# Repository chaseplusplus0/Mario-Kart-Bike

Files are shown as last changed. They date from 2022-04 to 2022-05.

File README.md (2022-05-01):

# MarioKart Bike Executive Summary

The MarioKart exercise bike project was an attempt to create an enjoyable and practical method of combining the benefits of aerobic exercise with the fun of playing a racing video game. The idea was to make physical activity easier and more desirable through the medium of gaming in a notably novel way. Using various external control systems attached to a standard bicycle, the goal was to turn a bike into a resistive-style exercise machine and a modified Nintendo Switch controller. The main functions desired for this system included functional steering translation, tire acceleration/RPM measurement, convenient buttons for other game functions (i.e. drifting, braking, item usage, menu navigation), and a microcontroller driven resistive element for the exercise portion. Ideally, these would all function with minimal user intervention so that the player can simply connect the controller and begin racing. The placement of the control options and various systems on the bike would be in safe, out of the way locations such that the user would not need to worry about any connections, mechanical obstacles, or malfunctions when using the bike in the standard fashion. Additionally, there was a design in place for an integrated health monitoring system to aid the user in finding out calories burned during play. The system as a whole was meant to be simple and streamlined such that almost anyone could hop on and start playing quickly.

# Current Capabilities

As of the latest contributions to the repo, the project functions minimally in all fields. Each subsystem planned in the design drafts has been implemented in some recognizable form. The capabilities of each system can be found in their individual files with much more detail.

### Controls

The control systems for steering, acceleration, drifting, and item throwing are all in place and playable. They are of high enough fidelity that consistently playing and winning competitive races is very much possible with a little practice. The connection is with the Nintendo Switch over bluetooth, and once connected the bike can be used much like a standard Pro Controller. There are rudimentary menu buttons in place on the RPi touchscreen for navigation, but their functions is not yet complete. Current menu navigation must be done via the touchscreen of the Nintendo Switch.

### Resistance

The resistance subsystem has gone through many different iterations of design and testing. The one contained within the repo governs a quick-switch relay setup that causes a very brief short in the leads of the motor, acting as a quick brake force which slows the user down. The intention was to have this trigger during certain in-game events, but due to difficulty reading game/vibration data back from the console, this is done at random intervals.

### Health Monitoring

The health system functions according to an MET equation that takes in the user's weight and the length of time activity is being performed. The user enters the information and starts a timer via an RPi touchscreen GUI and then stops the clock when the race is finished, after which they can obtain the caloric burn data.

# Salient Outcomes

The most important outcomes of the final version of this project include the functional control scheme, the basic resistance system, and the basic health system. These systems represent the core intentions of the project itself. The control system works perfectly well to play a race in-game. Steering, acceleration, drifting, and item throwing are all present and work great, allowing for an entirely plausible simulation of a controller. The resistance system is subtle, but effective at forcing the user to pedal a bit harder in certain stages. This in addition to the base resistance introduced by connecting the motor to the flywheel driven by the bike tire creates a solid workout that isn't too difficult to play through multiple races with. Additionally, it has been noted that most people hardly notice the exercise during gameplay due to being distracted by the enjoyment of the game, only mentioning the burn afterwards. This was one of the major goals of the project in general. Lastly, the MET health system is simple to operate and informative, making the process of calorie burn estimation easy for the user to gauge if desired.

# Video Demonstration and Photo Documentation

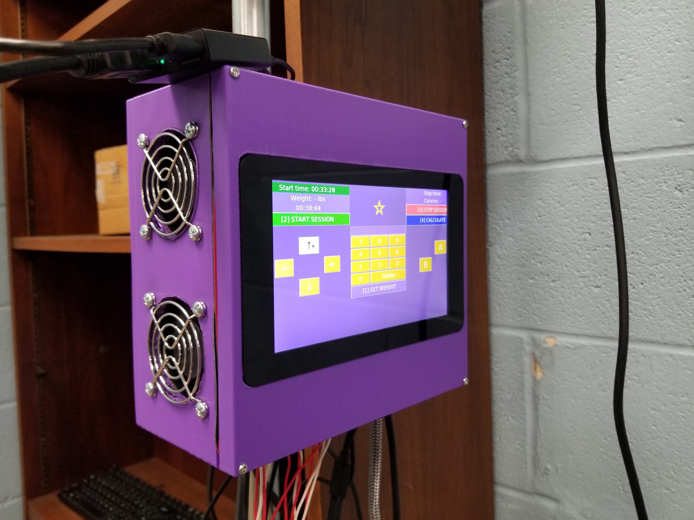
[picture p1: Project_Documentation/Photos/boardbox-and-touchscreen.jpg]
Video Video Demo (https://drive.google.com/file/d/1XO-LJ3wKvhisHmPTuDnR830Og8hAM-FM/view?usp=sharing)


Click the above picture to see the video demonstration of the project.

# About us

This was a 3 person capstone project at Tennessee Technological University that took place over the course of two semesters of class. Team members include Reed Hester, Leah Faulkner, and Chase Griffin. Reed Hester is an Electrical Engineer and a graduating senior, and he worked mostly on the physical frame, modelling, and resistive element of the design. Chase Griffin is a Computer Engineer and also a graduating senior, and he worked on developing the control systems, implementing the component and sensor systems on the bike, and writing the programs to both operate and control the components and communicate with the Nintendo Switch/MarioKart game. Leah Faulkner is also a Computer Engineer, and she worked on the MET health system equations, touchscreen GUI controls, and the board box fan/airflow improvement. The supervising faculty member on this project was Jesse Roberts, and he proposed the original idea for the project itself. There was no direct customer for this project, and the intended userbase was very broad.

# Repo Contents

This repository contains various bits of code used in the Mario Kart Bike capstone project. There are two Arduino files, one python program for the GUI, and one larger python program that collects data from every external system and converts it to controller data.

### Arduino Files

There are two Arduino compatible programs created for the two Arduino Nanos utilized in this project. The tachometer program contains the code necessary to operate the IR object-detection unit and to calculate the RPM from said unit. The motor control program contains the code to run the relay-controlled motor resistance system.

### MET and GUI Program

There is a python program that contains the code for the GUI that operates the health system and the menu navigation buttons.

### Joycontrol Python Program

This program is what does the actual control translation from each of the control systems on the bike. It is based on the open-source "Joycontrol" github program which can be found [here](https://github.com/mart1nro/joycontrol).

However, a specific branch was used for the applications of this project, which can be instead found [here](https://github.com/Poohl/joycontrol).

### Project Reports

The reports from the project proposal and phase 1 and 2 of design are contained in this repo in pdf form to give perspective on the entire design process from start to finish. They outline each step from conceptualization of the subsystems and initial specifications to the final version of each component and sensor being used in the build. It also contains the rationale behind each design choice, why some portions were removed from the scope, and why the bike exists in the state it does currently.

### Datasheet

There is a datasheet containing the interface and control details of each subsystem and how they interact with each other. It can serve as a general outline for how to use the system itself. There is also experimental data for each system present as well.

### Design Artifacts and BOM

The 2D schematics and 3D models used in the development of this project are also included as well to give a perspective on what was involved in the design process. There is a bill of materials that also shows the cost of every relevant component and structure used.

### Photos and Video

There are some pictures of the bike and its various components as well as a video of the completed project in working form.

# Final Notes

If there are any questions regarding certain parts of the bike construction or code function, please feel free to reach out here on Github or email me (Chase) at: chgriffin13@gmail.com

I'll do my best to help clarify!

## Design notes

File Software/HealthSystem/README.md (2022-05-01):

# What does it do?

This program generates the GUI for the MET health system and menu navigation buttons. It creates a graphical layout for the RPi touchscreen with several buttons, a keypad, and several display labels that allow the user to enter data for the caloric burn calculation as well as achieve basic menu navigation in the game during menu sequences.

# Dependencies

This program was written in Python 3 using the Tkinter toolkit to build the GUI. Tkinter is a part of the Python 3 library by default. It was written and formatted explicitly for the RPi 7" touchscreen module, but it can work without it using the desktop RPi controls.

# Installation

To install this program, simply clone the file and make sure Python 3 is installed on the computer. Additionally, if using the touchscreen, make sure the driver is up to date.

# Usage

To use, ensure the touchscreen is connected to the RPi, and then run the program. The GUI can be moved into place in the middle of the screen manually from the desktop if it does not fit. The RPi should also have a calibration feature in the settings if the touch does not seem to be in the right place. The keypad and corresponding weight and age buttons allow user data entry. The start and stop buttons control the timer. The calculation is performed on the stop of the timer. When using for a race measurement, simply enter the weight and age data, and then start the timer at the beginning of the race. When the race is over, hit stop, and your calorie burn count should be displayed. The menu buttons work like the standard d-pad and a/b buttons of a controller and can be used as such when connected to the game. Make sure all of the jumpers on the RPi are connected on the right pins to ensure these buttons will work.

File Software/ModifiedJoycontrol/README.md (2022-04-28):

# What does it do?

This file contains the modified version of the "Joycontrol" program used in our project. It serves as the primary control signal compiler, translator, and transmitter between the external control systems and the console/game. It runs on the RPi and connects to the Nintendo Switch via bluetooth. It is meant to simulate the datastream from a standard pro controller such that the Switch recognizes it as one.

# Dependencies

There are several dependencies to get this program working properly. First of all, it is only configured to run on the RPi 3/3B+ and cannot be guaranteed to work on other RPi device (although it technically should). It is running on the Raspian (RPi OS : Rapsian GNU/Linux 11 (bullseye)) Operating System. It also requires python3 to run the program itself as that is the language used for almost all files.

**Python** : [www.python.org/downloads](www.python.org/downloads)

As far as the libraries used within the program, many of them are detailed in the original README contents below, but there are a few additional ones required for the modifications.

If you don't already have pip:

	sudo apt install python3-pip

**GPIO Zero** : [Documentation](https://gpiozero.readthedocs.io/en/stable/index.html)

In RPi terminal:
	
	sudo apt update
	sudo apt install python3-gpiozero

**ADS1015 ADC library** : [https://github.com/adafruit/Adafruit_Blinka](https://github.com/adafruit/Adafruit_Blinka)

In RPi terminal:

	sudo pip3 install Adafruit-Blinka

Libraries in code:
	
	import board
	import busio
	import adafruit_ads1x15.ads1015 as ADS
	from adafruit_ads1x15.analog_in import AnalogIn

**Pyserial** :

	python3 -m pip install pyserial

Libraries in code:

	import serial

INSTALLATION AND USAGE PARAMETERS DEFINED BELOW

# Original README Contents
***

# joycontrol

Branch: master->amiibo_edits

Emulate Nintendo Switch Controllers over Bluetooth.

Tested on Raspberry 4B Raspbian, should work on 3B+ too and anything that can do the setup.

## Features
Emulation of JOYCON_R, JOYCON_L and PRO_CONTROLLER. Able to send:
- terminal button commands
- stick state
- nfc for amiibo read & owner registration 
- GPIO and serial compatibility
- Touchscreen button integration

## Installation
- Install dependencies  
  Raspbian:
```bash
sudo apt install python3-dbus libhidapi-hidraw0 libbluetooth-dev bluez
```
  Python: (a setup.py is present but not yet up to date)  
  Note that pip here _has_ to be run as root, as otherwise the packages are not available to the root user.
```bash
sudo pip3 install aioconsole hid crc8
```
 If you are unsure if the packages are properly installed, try running `sudo python3` and import each using `import package_name`.

- setup bluetooth
  - [I shouldn't have to say this, but] make sure you have a working Bluetooth adapter\
  If you are running inside a VM, the PC might but not the VM. Check for a controller using `bluetoothctl show` or `bluetoothctl list`. Also a good indicator it the actual os reporting to not have bluetooth anymore.
  - disable SDP [only necessary when pairing]\
  change the `ExecStart` parameter in `/lib/systemd/system/bluetooth.service` to `ExecStart=/usr/lib/bluetooth/bluetoothd -C -P sap,input,avrcp`.\
  This is to remove the additional reported features as the switch only looks for a controller.\
  This also breaks all other Bluetooth gadgets, as this also disabled the needed drivers.
  - disable input plugin [experimental alternative to above when not pairing]\
  When not pairing, you can get away with only disabling the `input` plugin, only breaking bluetooth-input devices on your PC. Do so by changing `ExecStart` to `ExecStart=/usr/lib/bluetooth/bluetoothd -C -P input` instead.
  - Restart bluetooth-deamon to apply the changes:
  ```bash
    sudo systemctl daemon-reload
    sudo systemctl restart bluetooth.service
  ```
  - see [Issue #4](https://github.com/Poohl/joycontrol/issues/4) if despite that the switch doesn't connect or disconnects randomly.

## Command line interface example
There is a simple CLI (`sudo python3 run_controller_cli.py`) provided with this app. Startup-options are:
```
usage: run_controller_cli.py [-h] [-l LOG] [-d DEVICE_ID]
                             [--spi_flash SPI_FLASH] [-r RECONNECT_BT_ADDR]
                             [--nfc NFC]
                             controller

positional arguments:
  controller            JOYCON_R, JOYCON_L or PRO_CONTROLLER

optional arguments:
  -h, --help            show this help message and exit
  -l LOG, --log LOG     BT-communication logfile output
  -d DEVICE_ID, --device_id DEVICE_ID
                        not fully working yet, the BT-adapter to use
  --spi_flash SPI_FLASH
                        controller SPI-memory dump to use
  -r RECONNECT_BT_ADDR, --reconnect_bt_addr RECONNECT_BT_ADDR
                        The Switch console Bluetooth address (or "auto" for
                        automatic detection), for reconnecting as an already
                        paired controller.
  --nfc NFC             amiibo dump placed on the controller. Equivalent to
                        the nfc command.

```

To use the script:
- start it (this is a minimal example)
```bash
sudo python3 run_controller_cli.py PRO_CONTROLLER
```
- The cli does sanity checks on startup, you might get promps telling you they failed. Check the command-line options and your setup in this case. (Note: not the logging messages). You can however still try to proceed, sometimes it works despite the warnings.

- Afterwards a PRO_CONTROLLER instance waiting for the Switch to connect is created.

- If you didn't pass the `-r` option, Open the "Change Grip/Order" menu of the Switch and wait for it to pair.

- If you already connected the emulated controller once, you can use the reconnect option of the script (`-r <Switch Bluetooth Mac address>`). Don't open the "Change Grip/Order" menu in this case, just make sure the switch is turned on. You can find out a paired mac address using the `bluetoothctl paired-devices` system command or pass `-r auto` as address for automatic detection.

- After connecting, a command line interface is opened.  
  Note: Press \<enter> if you don't see a prompt.

  Call "help" to see a list of available commands.

## API

See the `run_controller_cli.py` for an example how to use the API. A minimal example:

```python
from joycontrol.protocol import controller_protocol_factory
from joycontrol.server import create_hid_server
from joycontrol.controller import Controller

# the type of controller to create
controller = Controller.PRO_CONTROLLER # or JOYCON_L or JOYCON_R
# a callback to create the corresponding protocol once a connection is established
factory = controller_protocol_factory(controller)
# start the emulated controller
transport, protocol = await create_hid_server(factory)
# get a reference to the state beeing emulated.
controller_state = protocol.get_controller_state()
# wait for input to be accepted
await controller_state.connect()
# some sample input
controller_state.button_state.set_button('a', True)
# wait for it to be sent at least once
await controller_state.send()
```

## Issues
- Some bluetooth adapters seem to cause disconnects for reasons unknown, try to use an usb adapter or a raspi instead.
- Incompatibility with Bluetooth "input" plugin requires it to be disabled (along with the others), see [Issue #8](https://github.com/mart1nro/joycontrol/issues/8)
- The reconnect doesn't ever connect, `bluetoothctl` shows the connection constantly turning on and off. This means the switch tries initial pairing, you have to unpair the switch and try without the `-r` option again.
- ...

## Thanks
- Special thanks to https://github.com/dekuNukem/Nintendo_Switch_Reverse_Engineering for reverse engineering of the joycon protocol
- Thanks to the growing number of contributers and users

## Resources

[Nintendo_Switch_Reverse_Engineering](https://github.com/dekuNukem/Nintendo_Switch_Reverse_Engineering)

[console_pairing_session](https://github.com/timmeh87/switchnotes/blob/master/console_pairing_session)

[Hardware Issues thread](https://github.com/Poohl/joycontrol/issues/4)

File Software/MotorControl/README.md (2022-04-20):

# What does it do?

The motor resistance control program is incredibly simple. It has gone through many iteration, and some skeleton code from the old systems remains in comments in case those systems are ever revisited. Currently, the operating code governs a relay connected to the leads of the DC motor. This program quickly closes and opens the relay at random time intervals (between 10 and 45 seconds). It was meant to only trigger upon recieving serial data from the RPi that contained the vibration state of the controller recieved from the game. This condition, however, turned out to be redundant because the vibration state returned was always high, meaning the trigger happened repeatedly at all times. To save serial bus space for the RPi, this condition was removed, and now the trigger happens simply randomly.

# Dependencies

This program was designed for the Arduino Nano and a relay component. Without modifying pin connections, it will only work with these components. All functions present are found within the Arduino IDE. It is programmed in C++.

# Installation

To install this program, just open the Arduino file in the IDE, connect the Arduino Nano via USB to your computer, select the right board and port settings in the IDE tools, and then flash the board with the program.

# Usage

To use, make sure the program is flashed onto the Nano and that the pin connections are all done correctly. Next, make sure the relay is connected to the two motor leads such that closing it creates a short between the leads. Changing the delay between digitalwrite's can change the amount of time the leads are shorted form, however the time is currently at its minimum in the program. If using the serial line, make sure the Nano is only reading serial data, and use the read input as the condition for vibration data.

PIN CONNECTIONS (NANO to RELAY)  
5V to +  
GND to -  
PIN D6 to IN

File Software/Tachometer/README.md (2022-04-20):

# What does it do?

The tachometer program is pretty straightforward. It basically contains a delay-style function that counts the number of times an object was detected by the component. After a certain time period (about 3 seconds), the 
RPM calculation is performed and the RPM value is sent over the serial data line. There, it is recieved by the RPi and used to determine acceleration in-game.

# Dependencies

This program was designed for the Arduino Nano and the KY-032 IR obstacle avoidance sensor. Without modifying pin choices and connections, it will only work with these components. All functions used are present within the Arduino IDE. It is programmed in C++.

# Installation

To install this program, just open the Arduino file in the IDE, connect the Arduino Nano via USB to your computer, select the right board and port settings in the IDE tools, and then flash the board with the program.

# Usage

To use, just make sure it is flashed onto the Nano and that the pin connections are all done correctly. Then, make sure the KY-032 is facing the rotating object and that the LED brightness potentiometer is tuned to the right distance needed. Also, make sure that the serial is writing only the RPM (don't print anything else and don't use println) and that it is writing at 9600 baud rate (if you change this make sure to change it in the RPi serial read as well). The serial connection can be done directly from the Nano to the RPi.

PIN CONNECTIONS (NANO to KY-032):  
5V to +  
GND to -  
PIN 2 to OUT  
OPEN on EN

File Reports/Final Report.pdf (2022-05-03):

# ECE 4961- Group 2 - MarioKart Bike Final Report

Reed Hester, Chase Griffin, Leah Faulkner ECE Students, Tennessee Technological University Cookeville, TN, United States of America lrhester42@tntech.edu, cagriffin42@tntech.edu, lmfaulkner42@tntech.edu

Abstract --- This report introduces group two’s project idea and how it was implemented. An introduction of the problem begins the report, followed by the literature review, methodology, results and discussion, timeline and cost, ethics, lessons learned, and conclusions.

Keywords --- Capstone Design, gaming, emulation, exercise, sensors, electromagnetics, engineering

I. INTRODUCTION
A. Background
The Mario Kart exercise bike project is the result of an idea to bring physical activity together with the excitement of the racing video game experience. The objective with this idea is to design and develop a practical way to exercise using the traditional resistive elements of an exercise bike while simultaneously controlling a player in a game of Mario Kart in a simple-to-use, responsive, and enjoyable way. By using the bike as a direct controller, the player will be able to play as fluidly as they could with a standard controller with the added benefit of physical activity. Ideally, the bike will serve as a tool to assist in promoting a healthy lifestyle in an entertaining way.
To achieve this goal, the use of several external control systems combined with the inputs from a standard game controller will be employed. Microcontrollers with code interfaces set up to specifically target the operations for each subsystem of the controls will be utilized as well. These powered subsystems will consist of an adjustable resistance method, a pedaling speed sensing system, an encoded steering system, and an actual standard game controller. The resistance method will vary between two experimental versions of the bike. One method will consist of a magnetic resistance system involving a linear actuator that can incrementally increase or decrease the physical distance of a magnet from the bike wheel, thus creating dynamic resistance based on said distance. The other method of resistance is to use a DC motor connected to a MOSFET that allows the motor to be shorted on command, which creates resistive force when the motor is being spun. The pedaling sensor system will involve a tachometer sensor that measures the speed of the revolving pedals and uses that information to control the acceleration of the player’s vehicle. The steering mechanism will govern a rotary encoder which will be used to interpret directional controls. Finally, in order to simplify menu navigation and other game interactions, a standard game controller will be included as well with the traditional button layouts and usage. Each of the sub-microcontrollers in these systems will be routed into a main microcontroller or RaspberryPi device that interprets the received data into usable control information that is forwarded to the device running the game. The game version itself will initially be the Nintendo64 copy running on an emulator program contained on a PC. These design choices have been made out of a combination of the apparent ease of use and design. The use of an emulator software will only be for testing purposes in order to verify the operation of all control systems and will not be used for distribution or copying of the game software or license. An official copy of the game will be employed in the final product. In order to be practical and efficient, the systems on the bike must be simple to understand for the user, easy to access for a varied user base, safe to operate while still being an effective exercise tool, and responsive enough to allow reasonably quick game control.
The measures used to determine the success and achievement of the specifications will vary for each subsystem. Some of them, such as the control accuracy and ease of use, can be qualitatively assessed through regular use. Analytically, MATLAB, LTSpice, and Simulink simulations will be used for the DC motor circuit, the magnet setup, and the pedaling system. Also, control fidelity and response time can be measured using input lag detection software.
B. Motivational Analysis
Imagine yourself blazing down the road as your favorite Mario Kart character, racing and drifting through your favorite tracks, dodging rogue shells and bananas that litter the course, and finally sailing past the finish line just millimeters away from that other player who has been right on your tail since the start. An activity unlike most others, this kind of game inspires a competitive and energizing rush in many players. While most everyone can agree that games such as this are a highly mentally engaging experience, excessive gaming, and a correspondingly sedentary lifestyle, however, can actually be quite dangerous to one’s physical health over time. According to the CDC, adult obesity prevalence in the U.S. from 2017-2018 was found to be approximately 42.4% of the population, and has been shown to be steadily increasing since then [1]. While this is not necessarily directly linked to exercise habits, incorporating basic aerobic activity even without diet or routine change otherwise is proven to aid in weight loss and general health improvement [2]. However, many people find going to the gym, or rather exercise in general, to be too much effort, too inconvenient, too difficult, or just plain boring. Whatever the reason, If one could combine that great excitement and enjoyment that, as previously mentioned, often comes with their favorite video games with the extensive benefits of physical activity, it could likely make exercise a much simpler process that people would feel more readily willing to participate in.
The objective for this project is to develop a system that integrates basic physical exercise with the process of playing a video game, and the end goal is to create a fun and enjoyable way to work out while gaming in order to inspire gamers or other casual groups to fit more physical activity into their day-to-day routines to ultimately improve the general health of society. From these ideas, a logical first plan would be to utilize exercise equipment to control the game itself. Using an exercise-bike style system, the idea being proposed here is to connect the bike to the game in such a way that pedaling and steering motions from the user are tied to the standard control systems of accelerating and steering in Mario Kart. Additionally, feedback from the game itself, such as race speed choice or the act of being struck by an item or obstacle, will be used to affect the resistance against pedaling in varied ways. This is the basic plan for how the whole system will work, and in the following sections, this document will describe in more detail the specifications, constraints, and background behind this system as well as who this team consists of, our skills and resources, and the timeframe in which the development should take place.
C. Problem Formulation
i) Objective
One of the biggest cons of gaming is a lack of physical activity. Most games are played in a seated position with no activity besides small wrist and finger movements. Our objective is to merge exercise with gaming in an enjoyable and practical way, and our approach is through a piece of equipment the majority of people can operate: a stationary bike. To us, the most logical game to pair with such a system is a game involving vehicles. We’ve chosen Mario Kart because it is a well-known and loved game that all ages can enjoy.

ii) Specifications
The end goal is to build a system that allows the player to immerse themselves in the Mario Kart experience. Therefore, many modifications must be made to meet this goal. Physically, the system must support a wide range of ages and sizes. It must also be stable and comfortable for long gaming sessions. The system must be adjustable in order to provide the rider with varying levels of pedaling difficulty. The handlebars must be able to freely move left or right to provide steering, potentially with some resistance for realism.
Electronically, the system must be able to communicate with either an existing gaming system or a game emulator on a PC. The action of pedalling the bike should tell the game’s character to “go” and a rate of pedaling under a certain threshold should tell the character to “stop”. Potentially, the resistance of the pedaling could be adjusted electronically for a more seamless experience. Situations like difficulty selection and “crashing” should cause the bike to be harder to pedal. The handlebars should also be equipped with appropriate buttons for actions such as drifting, shooting projectiles/using items, and selecting menu items. If needed, the system should draw power either from batteries or from a standard 120V electrical outlet. Ideally, the system should also apply some sort of regenerative power option if possible. This, combined with low power components, will keep the whole thing as power efficient as achievable.
Safety wise, the system should be calibrated so that there are no sudden changes in resistance that could potentially cause injury. Instead, some ideal gradual rate of change would be the best choice and can be determined through consistent testing. Additionally, there should be some fail-safe in place for the pedal system in case the resistance suddenly gives out, again in the interest of preventing injury. It should be robust enough to handle forceful pedaling while still protecting the user from quick changes in difficulty.
D. Constraints
With the specifications and background in mind, there are constraints that must be followed to make the project successful. The system must be housed entirely within or on the stationary bike. No component may be located away from the bike assembly for a more minimalist look. Wires coming out of the bike should be kept to a minimum for both aesthetics and safety. Controls not related to driving or steering should be located on the handlebars for easy access to the user. The pedaling system must be able to withstand the torque produced by an average cyclist. Additionally, the resistance system must be able to handle rapid changes. As far as controls, accessing and modifying game code or memory while running may prove too difficult a process even through the emulator, so external control systems or alterations to already existing controllers may be the only feasible options. If necessary, the user may need to make the initial base resistance choice separately from race speed choice due to this issue. Since this bike would most likely be operated in a gym or other public setting, it would be powered ideally by a standard wall outlet, meaning the system needs to comply with the power rating and safety standards accordingly. Below is a list of known safety standards concerning the project.
a) Electromagnetics
- 299 - IEEE Standard Method for Measuring the Effectiveness of Electromagnetic Shielding Enclosures
- 299.1 - IEEE Standard Method for Measuring the Shielding Effectiveness of Enclosures and Boxes Having all Dimensions between 0.1 m and 2 m
- 1309 - IEEE Standard for Calibration of Electromagnetic Field Sensors and Probes, Excluding Antennas, from 9 kHz to 40 GHz
- C63.2 - American National Standard for Electromagnetic Noise and Field Strength Instrumentation, 10 Hz to 40 GHz Specifications

- C63.14 - American National Standard Dictionary of Electromagnetic Compatibility (EMC) including Electromagnetic Environmental Effects (E3)
- C95.1 - IEEE Standard for Safety Levels with Respect to Human Exposure to Electric, Magnetic, and Electromagnetic Fields, 0 Hz to 300 GHz
b) Electronics
- NESC HBK - National Electrical Safety Code (NESC) Handbook
c) Batteries
- 946-2020 - IEEE Recommended Practice for the Design of DC Power Systems for Stationary Applications
E. Salient Outcomes
The most important outcomes of the final version of this project include the functional control scheme, the basic resistance system, and the basic health system. These systems represent the core intentions of the project itself. The control system works perfectly well to play a race in-game. Steering, acceleration, drifting, and item throwing are all present and work great, allowing for an entirely plausible simulation of a controller. The resistance system is subtle, but effective at forcing the user to pedal a bit harder in certain stages. This in addition to the base resistance introduced by connecting the motor to the flywheel driven by the bike tire creates a solid workout that isn't too difficult to play through multiple races with. Additionally, it has been noted that most people hardly notice the exercise during gameplay due to being distracted by the enjoyment of the game, only mentioning the burn afterwards. This was one of the major goals of the project in general. Lastly, the MET health system is simple to operate and informative, making the process of calorie burn estimation easy for the user to gauge if desired.
F. Report Structure
The structure of this report contains a review of the literature surrounding the topic of exercise bikes and their extended use in the gaming setting, the method of which the group has approached the problem outlined in the introduction in both the design and build choices, the qualitative and quantitative experimental results of our final version of the project after each subsystem was implemented, the timeline of progress and final cost of the actually construction and assembly of the design, all ethics considered during the project and all lessons learned after the fact, conclusions including possible future work, and lastly and appendix containing personal notes of contribution and skills acquired during the project all in that order. Each section is labeled accordingly. Any more information regarding specific details of the project can be found on the official Github repository.

II. LITERATURE REVIEW
Before addressing the MarioKart bike, it is necessary to explore what kinds of stationary bikes are on the market. Generally, there exists three types: upright, recumbent, and indoor cycles. Upright bikes hold the user in a vertical position, similar to a bicycle. They typically have smaller footprints because the pedals are below the seat. Next is recumbent bikes, which keep the user in a fully-seated position. The pedals are directly in front of the seat, allowing the user to relax the rest of their body and focus on pedaling their legs. Finally there’s indoor cycles, which closely resemble road bicycles. The handlebars are directly in front of the seat, meaning the user’s back is nearly parallel to the floor. While this position may seem less comfortable, most users report that this is the most realistic riding position that stays comfortable through long sessions [3]. All of these bikes have adjustable seats and can support around 250-300 pounds, making any of them suitable for our requirements
The above bikes are all constructed in the same basic fashion. The user sits on the seat and turns the foot pedals, just like a normal bicycle. The pedals are attached to a chain or belt, which drives a large flywheel. The flywheel is where the resistance of the pedaling is typically adjusted. There are several ways to add resistance to the system, but the two most common ways are through friction or magnetics. Friction bikes have a contact pad attached to a rod that the user can adjust. Turning a knob will move the rod up or down, causing the pad to be pushed into or pulled away from the flywheel. The benefit to these is that the knob includes an emergency stop feature where the user can push the rod all the way in and the contact pad forces the flywheel to stop spinning. Magnetic bikes work very similarly, with one key difference: there is no contact with the flywheel. Instead of a contact pad, a series of magnets is attached to the adjustable rod. The closer the magnets get to the flywheel, the higher the resistance becomes. This is due to a phenomenon called eddy currents. When a non-magnetic metal comes in contact with a magnetic field, eddy currents are produced in the metal. These currents flow perpendicular to the magnetic field, creating a friction-like resistance between the magnet and the metal [4]. What’s useful about this is that there is no actual contact or friction involved. This saves the materials from wear and greatly prolongs the lifespan of a magnetic bike. Magnetic resistance is highly adjustable and some bikes even come with an electromagnet that is electronically controlled, allowing the resistance to be adjusted by changing the strength of the magnet rather than its position. Either form of magnet resistance would be suitable for our purposes. One con of magnetic bikes is they are generally more expensive than other variants.
An uncommon way to add resistance to one of these stationary bikes is to attach the flywheel to a permanent magnet DC motor. A DC motor has two wires, positive and negative. By shorting/connecting these two wires, a force called back torque is created. Back torque is caused by the internal voltage created when the wires are shorted. When back torque is present, the shaft becomes harder to spin [5]. To control when the two wires are shorted, some kind of switch is required. A switch that is easily controlled by a computer is called a transistor. Transistors are essentially voltage controlled switches. When a signal is sent to one, the switch is flipped. One of the most common kinds of transistors used in small-scale electronics is called a MOSFET (Metal Oxide Semiconductor Field Effect Transistor) [6]. MOSFETs have 3 terminals: the source, the drain, and the gate. Current travels from the source, through the MOSFET, and out of the drain. When a certain voltage is applied to the gate, the MOSFET allows the current to travel through. A MOSFET acts as an open when there is no gate voltage, and as a short when there is voltage at the gate. By varying the voltage at the gate, the level of resistance between the source and drain can be changed. Higher voltage at the gate means lower resistance. With some sort of microcontroller, the gate voltage could potentially be controlled by the game.
Another common feature - or lack thereof - of stationary bikes is immobile handlebars. Some bikes come with an additional arm workout in the form of two handles that move with the motion of the flywheel, like an elliptical stepper machine. However, this kind of motion is not what this project requires. We need bicycle-like steering. With any stationary bike selection, modification would be required to allow for free steering. Most stationary bikes come with bent or vertical handlebars, which fortunately would provide our users with a more realistic riding experience.
To get the bike to communicate with the game, it needs switches, buttons, and sensors. Most of the hardware required comes conveniently packaged in video game controllers. Buttons to scroll through menus and select options, use items, and drive the Kart are readily available in these controllers. Additionally, these buttons are designed to be pressed often and be responsive since they are for gaming. To control the game, either an electromechanical or a computerized approach will be taken. In either case, a sensor to measure the speed or frequency of the rotating pedals will be needed. A tachometer is a sensor designed to measure the RPM (rotations per minute) of rotating objects. For this project, an optical tachometer would be suitable. These operate by shining a light, like an LED, against the rotating object. The light reflects off the surface back into the sensor, triggering a signal. The rate at which the signal is triggered is used to determine the RPM of the object [7]. Regarding the running of the game itself, it may prove difficult to use an actual console given how securely and privately Nintendo handles its proprietary systems. Therefore, for the purposes of this project, an emulator will be used in order to allow us to run the game client on a PC, which will give us greater options regarding interactions between the control system and the game data. An emulator is generally a piece of software that allows one computer to simulate the processes and conditions of another virtually identically. This allows the host machine to access programs and features that are typically only available to the system being emulated [8]. An emulator will allow more versatility to the type of controls available for usage in this project, as well as increased performance from the game itself as compared to the original console. Most emulation software designed for games provide the option to create a custom map of controls based on inputs received from the control system. This makes it quicker and easier to test and replace control options than that of a dedicated console. For the purposes of this project, the N64 version of Mario Kart will likely be used due to its relative simplicity and ease of emulation.
III. STANDARDS CONSIDERED
a) Electromagnetics
- 299 - IEEE Standard Method for Measuring the Effectiveness of Electromagnetic Shielding Enclosures
- 299.1 - IEEE Standard Method for Measuring the Shielding Effectiveness of Enclosures and Boxes Having all Dimensions between 0.1 m and 2 m
- 1309 - IEEE Standard for Calibration of Electromagnetic Field Sensors and Probes, Excluding Antennas, from 9 kHz to 40 GHz
- C63.2 - American National Standard for Electromagnetic Noise and Field Strength Instrumentation, 10 Hz to 40 GHz Specifications
- C63.14 - American National Standard Dictionary of Electromagnetic Compatibility (EMC) including Electromagnetic Environmental Effects (E3)
- C95.1 - IEEE Standard for Safety Levels with Respect to Human Exposure to Electric, Magnetic, and Electromagnetic Fields, 0 Hz to 300 GHz
b) Electronics
- NESC HBK - National Electrical Safety Code (NESC) Handbook
- IEC 60529 - Electrical enclosure protection
c) Batteries
- 946-2020 - IEEE Recommended Practice for the Design of DC Power Systems for Stationary Applications

IV. METHODOLOGY

i. INTRODUCTION
The MarioKart Exercise bike system is a device with the ultimate goal of offering an engaging and practical way to combine the benefits of physical activity with the fun and excitement of playing a video game. In order to achieve such a goal, a design that can communicate the user’s motion into utilizable control data is required. It must also offer a similarly fluid experience in controlling the game as one would find with a typical game controller. To be viable for the average consumer, the design must be modular enough to be applicable to a standard bicycle design and non-invasive enough to the original frame to be easily assemblable. Above all, it should also maintain the safety and comfort of the user during operation as well.
The system has been broken down within this document into several functional subsystems, each with a specific purpose relevant to the goals previously outlined. The diagram below represents the conceptual structure of the project as a whole.

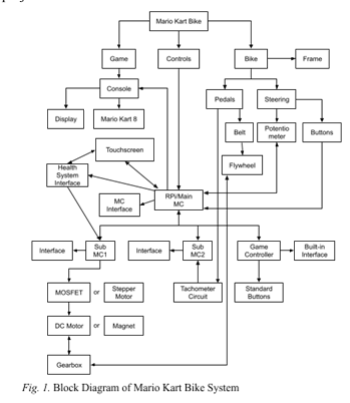
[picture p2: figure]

As shown in the block diagram, the system will ideally have two versions: a DC Motor resistance system and a traditional magnetic resistance system. The rest of the subsystems on these bike designs will be exactly the same, with the only experimental variable being the method of resistance generation. A conceptual diagram with the location of each general connection between subsystems is shown below.

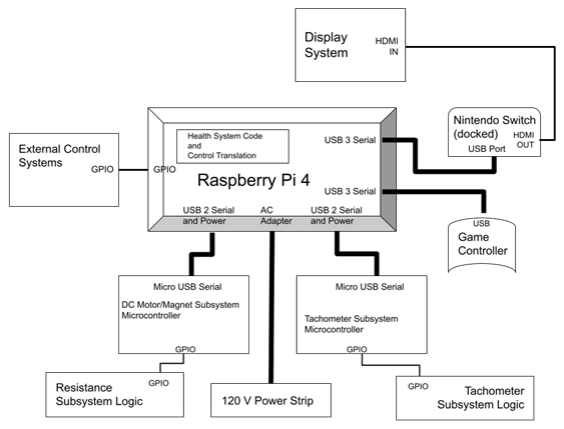
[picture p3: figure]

Fig. 2. Conceptual System Diagram

ii. GAME SYSTEM

A. PC Subsystem
i) Running the Game
In order to run the game software itself, the project requires either a video game console or some form of emulation (i.e. running the game through emulation software on a personal computer). The decision was made to use the Nintendo Switch console to run the game, due to potential copyright issues pertaining to emulation. Additionally, the Nintendo Switch provides access to the latest version of MarioKart, which will allow users to enjoy the most up-to-date experience of the franchise.

ii) Displaying the Game
In terms of video and audio output, the Nintendo Switch console that is running the game will be connected to two PC Monitors via an HDMI splitter. This will allow two players to view the same game session on two different bikes with separate monitors. Therefore, the players will be able to play together in real time as they normally would in-game. In addition, there will be a touchscreen display that serves as both a monitor for the health system and a selection menu for certain game and bike functions. The monitors and HDMI cables have already been freely obtained. The only component on the bill of materials for this system will be the splitter.

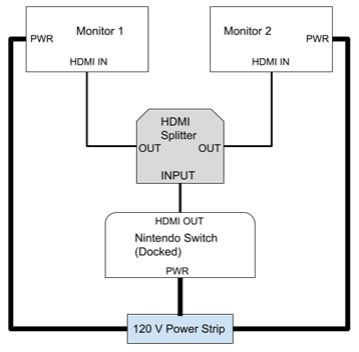
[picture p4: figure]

Fig. 3. Display Schematic

iii. CONTROLS SYSTEM
The purpose of the controls system is to provide a means for the player to use their bicycle to play MarioKart. The system must interpret various mechanical inputs, like pedaling and steering, while also providing feedback to the player in the form of dynamic pedaling resistance. It must also contain all of the necessary control options to cover each in-game action like a standard game controller would. The system must also be modular for ease of replacing components.
A. Main Microcontroller
The main microcontroller in this design needs to cover both the control of data to and from the subsystems and the translation of signals into usable control data. Additionally, certain peripheral components for other game control purposes will be connected directly to the main microcontroller and interpreted according to their associated function (e.g. initial resistance selection). These desired functions necessitate ample GPIO and serial data connections, as well as the ability to power said subsystems and components. In order to keep the design as compact and modular as possible, each of these constraints should be met by a single microcontroller system controlling a series of sub-microcontrollers with less complex and more specific duties. Each GPIO pin can supply up to 16 mA of current, with a maximum possible draw of 30 mA. Each of the sensors we will be using require less than this amount for proper operation. The 5V power rails are able to supply power directly from the connected power source. The main microcontroller selected to fulfill the general needs of the design and serve as the overarching manager for each subsystem controller is the Raspberry Pi 4 Model B: 4 GB memory version.

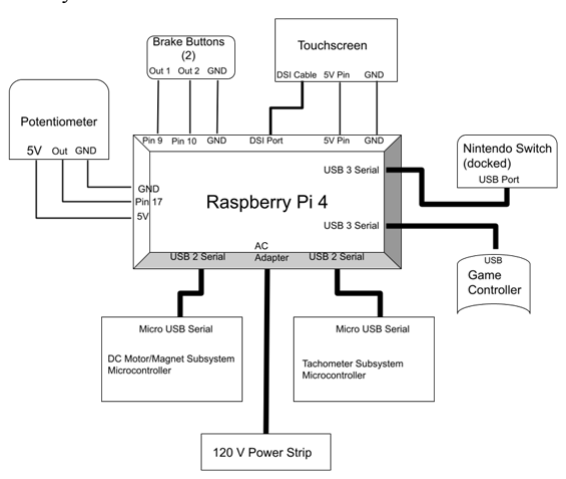
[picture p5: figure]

Fig 4. Raspberry Pi I/O Diagram

This version of Raspberry Pi (RPi) possesses two USB-2 and two USB-3 ports which will allow it to connect to both sub-microcontrollers through two separate data lines using mini-USB to USB Type A cables. This way, sensor information obtained from each subsystem and current game state information can be transmitted through serial data, and each sub-microcontroller can be powered from those same connections. Additionally, the RPi contains a 40 pin GPIO header with two 3.3 V and two 5.0 V power pins, 4 dedicated ground pins, and several custom function pins that will be used to manage both the external buttons and the touchscreen device which all require direct connection to the RPi. It also contains an AC adapter which allows it to be powered from a standard wall outlet.
Control translation will take place directly on the RPi as well. Because it will be receiving player activity data from each subsystem, the RPi’s primary purpose is to decipher the incoming signals and turn them into functional control information to be sent to the Nintendo Switch console and used for gameplay. There are several open-source, RPi-compatible libraries in existence that aid in the conversion of external data into control data (such as “NSGadget_Pi” which uses an RPi and other external electronic devices to impersonate a Nintendo Switch controller), and the RPi community has a large resource base of other programs with very similar functions that will help simplify the control operations as well.
B. Resistance Subsystem

i) Sub-microcontroller
The sub-microcontroller selected for both the DC motor and the magnetic resistance system is the Arduino Nano. This microcontroller contains two true analog outputs which are capable of outputting a voltage ranging from 0 to 5 V. Additionally, it contains 8 dedicated analog inputs that will be used to obtain feedback voltage and current values from the DC motor circuit. The fidelity of the digital-to-analog converter can be set to either 8 or 10 bits within the software. At the maximum fidelity of 10 bits, the user can adjust between 2^10 or 1024 partitions of voltage. Each partition modifies the voltage by approximately 4.883 mV. Though the analog input from the hall sensor will only reach approximately 0.7 V, an amplifier will be used to step this range up to 4 V, which leaves 819 partitions worth of fidelity. This should give the board an adequate degree of sensitivity for controlling the DC motor resistance system precisely enough to simulate a dynamic range of resistance settings that is both realistic and challenging to the user.

ii) DC Motor Resistance The DC motor will serve as the main form of resistance

for one of the bikes. Before choosing a motor to fit in this system, it's important to know what kind of load it will be receiving. Based on research, it has been found that the average person pedals a bike at 50-90 RPM with an applied torque of 30 ft-lbs. Since DC motors are built for the opposite (high speed and low torque), a gearbox will be needed to transfer the input from the pedals into what the motor can handle.
| Using AutomationDirect’s website, the team has found a
gearbox and motor combo that will meet the required specifications.. The gearbox is a 20:1 speed reducer, but if it is run from the output shaft, it becomes a 1:20 speed increaser. The output shaft can handle 345 in-lbs (28.8 ft-lbs) at 88 RPM. Although 28.8 ft-lbs is slightly less than 30 ft-lbs, this gearbox will work because it's rated for that torque at the higher end of a cyclist's RPM. As a cyclist increases their RPM, their torque will decrease.
| The chosen motor is a 0.33 HP permanent magnet direct
current (PMDC) motor that is rated to run at 1800 RPM. Since a 1:20 ratio was chosen for the gearbox, if the rider of the bike pedals at 90 RPM (an average person’s maximum effort) then they will match the rated RPM of the motor. The motor runs at 180 V with a peak current of 1.75 A, meaning the maximum power is around 315 W. The motor is sold in a 90 V variant as well, but the 180 V model was chosen because it has a lower peak current with the same power output. Average to healthy cyclists can produce anywhere from 100-300 W when pedaling, so this motor is rated to handle whoever drives it.
| The reason a PMDC motor was chosen is because they
have a constant current (at high RPM) and a variable voltage when used as a generator. The voltage has a linear relationship with the input RPM, while the current remains virtually constant once a certain RPM is reached. The speed increase from the gearbox ensures that the current will be in that constant range. The motor and gearbox are represented visually in the DC Motor Control section below.

iii) DC Motor Control The purpose of the circuitry around the DC motor is first

of all, to control the resistance across the positive and negative terminals, and second of all, to measure the voltage and current being generated by the motor during operation. In short, the resistance across the terminals will be controlled by an n-channel MOSFET, the voltage will be measured by an op amp configured as a diff amp, and the current will be measured by a hall sensor.
| The point of measuring the voltage and current at all
times is so that the performance of the MOSFET can be monitored. As the MOSFET is under operation, it will heat up. As the MOSFET heats up, it will become less conductive. To mend that, it will need a higher gate voltage. By monitoring the voltage and current being generated by the motor, the magnitude of that adjustment can be determined.
| The MOSFET will serve as the main control of the
connection between the positive and negative leads of the motor. Transistors in general are typically known as switching devices, where moving from a low state to a high state is the top priority. But for this use case, the MOSFET will be operated in its linear or ohmic region. Between the transition from low to high, there is a range of gate voltages that keep the MOSFET in a partially open/closed state. The goal here is to control the MOSFET with a microcontroller's analog output pin. That means the range of gate voltages for the ohmic region should be less than 5 V. The motor will be generating up to 180 V and 1.75 A during peak operation, so the MOSFET should be rated for such high parameters. The chosen MOSFET is rated for well over this use case, and the ohmic region is between a gate voltage of 3-5 V. The specific package being used is the TO 247.
| The protection diode included in the circuit is meant to
be a safe-guard. Under normal operation, the current will be coming out of the positive terminal of the motor. However, if the rider were to pedal the bike backwards, the polarity of the motor would be flipped. That means the current would flow in the other direction. To prevent damage to other components in the circuit (mainly the microcontroller), a diode needs to be added. If the current comes out of the positive terminal like it should be, then the diode will see no current. If the current comes out of the other terminal of the motor, then the diode will be fully conductive and keep all of the current in a loop with the motor. The chosen diode is rated for 400 V and 2 A with a forward voltage of 1.1 V. The MOSFET and diode make up the bare minimum requirements for controlling the DC motor. They are represented in Figure 5.

Fig. 5. MOSFET and Diode Circuit

The sub-microcontroller being used to control the MOSFET and collect the measurements of voltage and current is the Arduino Nano. This board has two true analog 5V output pins and several analog to digital input pins. The analog-to-digital (a2d) conversion happens on the board itself, and it has a configurable resolution. In the code, the programmer can set the fidelity to 8 or 10 bits. The team has chosen to use a 10 bit fidelity. 10 bits means 1,024 individual partitions. The pins can read signals up to 5V, which means there are 5/1,024 = 4.883 mV per partition. That's also 204.8 partitions per one volt. This will be a useful consideration because if the measurement devices can output a signal close to 5V, they can take advantage of the full resolution.
To measure voltage, an op amp will be connected across the positive and negative terminals of the motor. However, the 180 V being generated is too dangerous for most op amps and for the microcontroller. Therefore, the op amp needs to have a resistor network surrounding it that both protects its own inputs and configures the op amp into a differential amp. A network of four resistors can accomplish both tasks. By connecting the op amp in a negative feedback loop, it can be configured to have a gain less than one. That will be very important in stepping down the motor’s 180 V to 5 V or less so that the microcontroller can understand the measurement and be kept safe. Aiming for 5 V or less also ensures that the op amp will be taking advantage of the full resolution of 1024 partitions. It is also important that the inverting and non-inverting terminals of the op amp don't see too much voltage or current. With some circuit analysis, these specs can be met. By setting R1=R2 and R3=R4, the process becomes even simpler. Through nodal analysis, the following equations were generated:

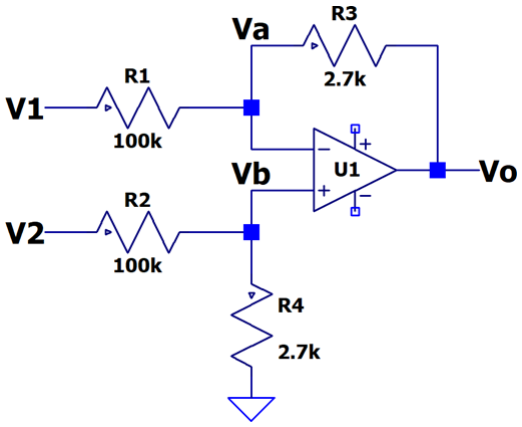
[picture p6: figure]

Fig. 6. Op Amp Voltage Measurement Circuit

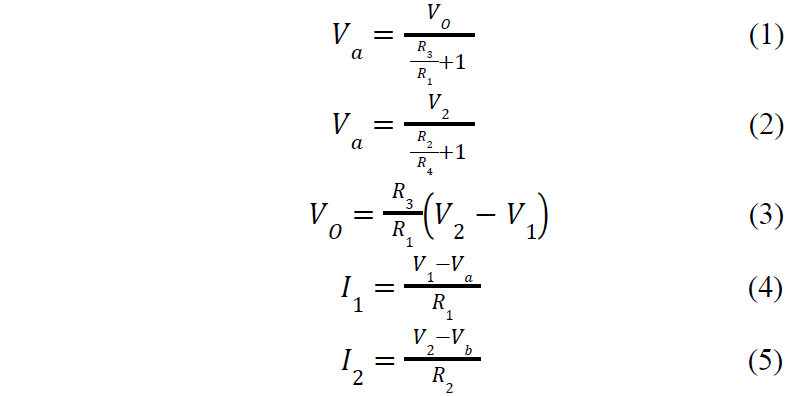
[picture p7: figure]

The measurement will be taken by connecting the positive terminal of the motor to V2 and the negative to V1. The most voltage V2 will see is 180 V, and the least V1 will see is 0 V. Vo needs to be 5 V or less, meaning the ratio of R3 and R1 can be solved for. It comes out to 0.0278. Additionally, in order to keep the current low, all of the resistors need to be in at least the kiloOhm range. I've chosen to make R3 and R4 2.7 kOhms and R1 and R2 100 kOhms. With those chosen, that means:

With those specs in mind, an op amp can be chosen. The team has picked the LM 741 op amp, which can handle up to 30 V at each terminal.
To measure current, the team has chosen to use a hall effect sensor. It will have to be able to measure up to 1.75 A and potentially handle high voltage. The chosen chip is meant to have the full load of current injected into it. It is built with a layer of insulation between the input pins and the rest of the internal hardware. The hall effect takes place through this layer of insulation. Only the magnetic field will travel through the insulation. Then, the chip will output a voltage proportional to the current it is receiving. The chip will output 400 mV per amp it reads. This will leave the output voltage well under 5 V for the microcontroller. It is an 8 pin chip and pins 1-4 act as the IN and OUTs for the current to travel through. The purpose of including 2 IN pins and 2 OUT pins is so that the current can be split and a smaller trace can be used on the PCB the chip is mounted to. In particular, the A4 model should be used because it can read a minimum of 125 mA and a maximum of 12 A. Since the chip outputs 400 mV per amp it measures, it will output a peak of 700 mV because the peak current of the motor is 1.75 A. To ensure that the resolution of the measurement is usable, the output of the hall sensor needs to be amplified. Since the resolution of the arduino's a2d conversion is 204.8 partitions per volt, if the signal is left unaltered, only 143.4 partitions will be available. The advertised peak current is 1.75 A, but just to be safe, it should be assumed that it could get higher. That means the chip's 0.7 V max should be amplified to around 4 V for safety. To accomplish this, another LM741 amplifier circuit will be implemented. The op amp will be configured as a non-inverting amplifier, which looks like this:

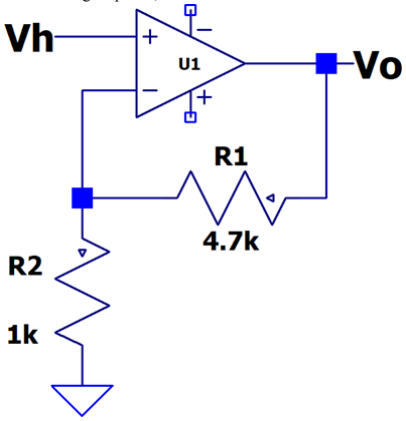
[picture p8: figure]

Fig. 7. Hall Sensor Preamp Circuit

Vh is the signal from the hall sensor, and Vo will be what is sent to the microcontroller. Vh has a typical maximum of 0.7 V, and to be safe, the op amp should output 4 V. That means the ratio of R1 and R2 should equal 4.714. If the maximum output is around 4 V, that means the resolution is 819.2 partitions. That's 80% of the maximum resolution.

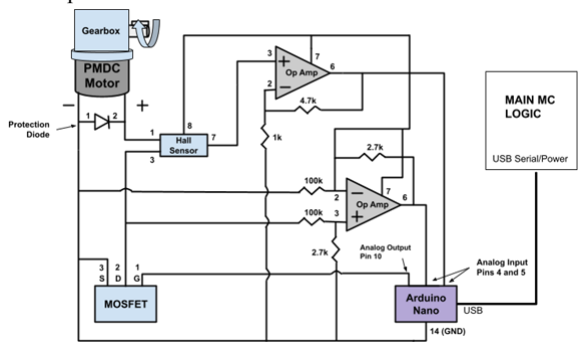
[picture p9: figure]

Fig. 8. Complete DC Motor Resistance Control Circuit

With all the components combined, the final circuit is shown above.

iv) PCB Design The PCB must serve as a solid structure to mount the

components of the circuit to and act as a conducting path for the appropriate connections. Sections of trace that are directly connected to the motor must be at least 40 mil in order to handle the max current of 1.75 Amps. There must be solder holes in places where a wire must be connected to the board. No connectors are necessary because the connections are meant to be permanent. The diagrams below show the layout of the PCB and highlight the trace connections.

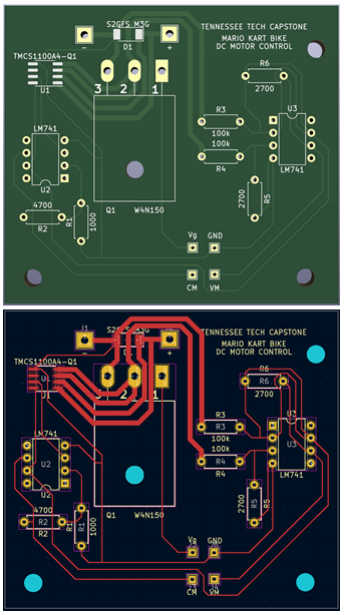
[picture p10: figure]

Fig. 9. PCB Design for the DC Motor Circuit

v) Magnetic Resistance
The magnetic system will serve as the main form of resistance for a second bike setup. The magnet must be electronically adjustable such that the distance between it and a flywheel can be modulated, and it must be able to provide resistance similar to what would be seen on various terrain inclines outdoors.
The most efficient method determined for use in the current bike design is to utilize a magnetic resistance component that is shipped along with the rear wheel frame, which will be shown in more detail later in the report. As for the magnetic component, it is essentially a magnet and flywheel working in tandem to provide resistance. It operates using eddy currents, the same principle used in designing auto-belay systems for climbers and repellers. There is a cable attached to the magnet that, when tensioned, moves the magnet closer to the flywheel. The closer these two get to each other, the greater the resistance.

vi) Magnet Control The controller for the magnet must be able to

electronically adjust the position of the magnet based on player preference and in-game factors. The current plan is to use a stepper motor to induce tension on the cable rather than the manual adjustment it ships with.

C. Tachometer Subsystem
i) Sub-microcontroller
| The sub-microcontroller selected for the tachometer
subsystem is also the Arduino Nano. This microcontroller is required to convert the signals from the tachometer component into RPM in order for that information to accurately serve as the acceleration control in-game. It also possesses the minimal GPIO needed to operate the tachometer through the power, ground, and data pins found on the board. Additionally, the acceleration signal will be pulse width modulated upon leaving the Nano, not by using the PWM pins, but rather through a calculation within the program to allow uniform communication through the USB serial data lines, in increasing frequency based proportionally on increasing RPM. This will allow for a smoother acceleration control experience that more closely resembles the real-life process of gradually gaining speed when accelerating on a bicycle.

ii) Tachometer Board For the tachometer component, this design necessitates

the ability to optically measure the rotational speed of either the pedaling from the bike user or the rotation of some other mechanism on the bike. It also needs to return some sort of signal indicating the measured RPM or otherwise a signal that can be interpreted as an RPM value through some calculation made outside of or on the selected device..
| The component that will serve as the optical tachometer
designated for use in this subsystem is the KY-032 infrared obstacle avoidance sensor. This component contains an IR LED and an IR-sensitive photodiode that is capable of detecting reflected light from the LED off of some sort of reflective surface. The output signal returned by the device can follow both TTL and CMOS logic, and it sends a low level if an obstacle is being detected or a high level if no obstacle is being detected. The device contains two potentiometers, one that controls the flashing frequency of the LED through the NE555 timing chip, and the other that controls the brightness of the LED which allows for indirect control of the distance of detection by the photodiode. The board contains 4 pins, one for ground, one for power, one for the logical output of the system, and one for enabling the device. The enable pin is unused as long as the jumper on the board is kept in place, therefore it is left open. The control circuit for this subsystem is shown below.

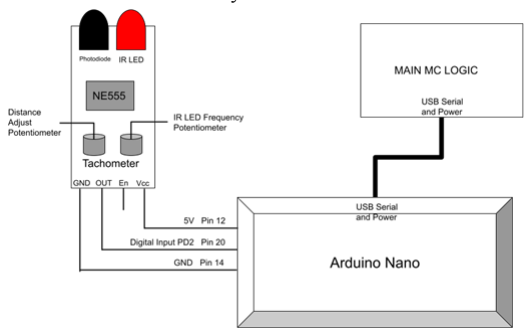
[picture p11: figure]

Fig. 10. Tachometer Control Circuit

The device's original intended function by the designer is to detect the IR light that the LED emits being reflected off of an object and subsequently signaling that an object has been detected in front of the device with a low logic signal. However, the true purpose of this device in this design is for use as an optical tachometer to measure the RPM of a spinning gear. This can be achieved by connecting it to the Arduino Nano and feeding it the detection data. Although this device is typically used to simply detect when an object is in front of it, the Arduino can be programmed to calculate RPM from the measurement. As previously stated, the component returns a logical low (~0 V) when the photodiode picks up reflected light from an object in front of it, and for a spinning object such as the pedals of the bike or the flywheel, it detects this signal multiple times with each pass of the object. The RPM can be determined from this by a simple calculation:

RPM = ((# of events * time interval of measurement) /
(# of objects in rotation))

"# of events" is how many times the component has signaled a detected reflection, "time interval of measurement" is how many times a minute the RPM has been sampled, and "# of objects in rotation" represents the number of objects that pass in front of the detector that are part of the same spinning apparatus (e.g. there 2 pedals on the bike, but only one spinning apparatus).
This component can be directly powered and controlled by the Arduino Nano with it’s digital GPIO pins and 5 Volt power pins, and it can perform all of the necessary
calculations | within | the | microprocessor | on-board.
Additionally, in order to achieve a more realistic acceleration control experience, the Nano can be used for pulse width modulation of the outgoing control signal in a way that causes gradual increase in speed rather than an all or nothing trigger.

The photodiode on the sensor has certain mechanisms to prevent signals that aren't intended for use from being picked up. This requires certain parameters to induce a desired logic signal that are outlined in the description below. The IR-sensitive photodiode used on this component is the HS0038B. It possesses a bandpass filter, an integrator stage, and automatic gain control to filter out noise or disturbances from the desired IR signal detection. In order
to | distinguish | a | true | data | signal from said
noise/disturbances, the signal received must be of or near the carrier frequency of 38 KHz, which is possible to achieve from the flashing LED using the tuning potentiometer and an oscilloscope to monitor the exact frequency as it is changed. Additionally, the reflected signal must be received in bursts of 10 – 70 cycles for optimal performance with a non-reflective gap time in between of at least 14 cycles. The datasheet for the device does not give an exact rise/fall time for the logic signal found at the output pin, however, the times for each component of the device are available. The circuit schematic of the device is shown in Figure 11 [9].

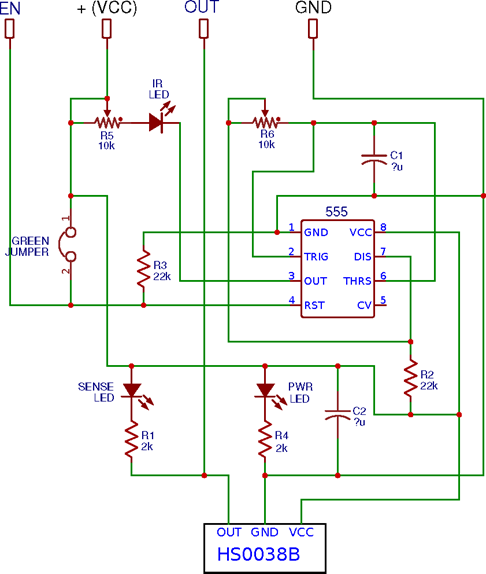
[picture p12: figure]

Fig. 11. Circuit Schematic of the Components on the KY-032 [9]
The only devices involved in the output logic signal are the HS0038B IR-Photodiode and the NE555 timing chip. The photodiode has a maximum rise/fall time of 100 nanoseconds, and the NE555 has a maximum rise/fall time of 300 nanoseconds, resulting in a total logic delay of 400 nanoseconds in a worst case scenario. At 38 KHz frequency, the LED will be flashing once every 26.316 microseconds. For 10 cycles to be achieved and including the initial fall time as the logic signal is set to low, the light must be reflected for at least 263.56 microseconds. The minimum gap time of 14 cycles will take up at least 368.824 microseconds of time, including the initial rise time as the logic signal is returned to high. Including these along with the dynamic response of the photodiode itself, this results in a minimum marginal total of 632.384 microseconds of operational time to achieve a sound logic signal. The object planned for use to measure RPM will be the gear of the bike itself with the holes and surface shrouded by a dark covering (black paper, tape, etc) and a white line on the covering to act as the reflective portion. The maximum estimated RPM for the gear when the bike is being used is approximately 90 RPM. This means there will be 1.5 rotations every second, or 0.6666 seconds per rotation. That equated to 666.66 milliseconds of time to work with in total for each rotation of the gear. Since only 632.384 microseconds (or 0.094%) of the rotation time is necessary for a functional logic signal, it will be simple to place a reflective strip of adequate width to both meet the minimum operational time needed and fit well onto the gear. Exact dimensions of the strip will be a minimum of 0.094% of the circumference of the gear in order to comply with this design. Figure 12 is a model of the design plan.

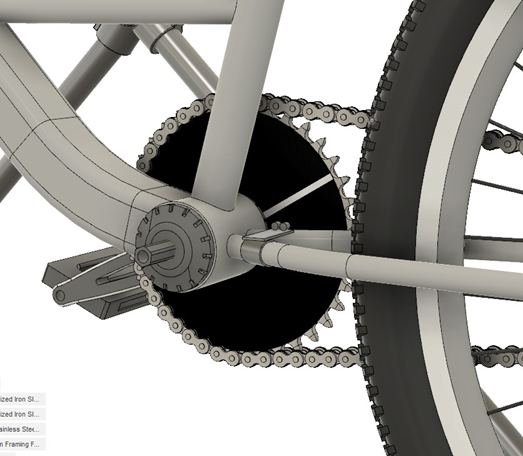
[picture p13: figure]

Fig. 12. Prototype CAD Model of the Tachometer Mounting Setup

The device is represented by the small gray plate and two cylinders in front of the pedal mount and is facing the gear. The gear has been shrouded with a black covering, and a white line, which will serve as the reflective patch for achieving the correct cycle count, has been placed on it. As the user pedals and the gear rotates, the white stripe will periodically pass in front of the device, causing the IR light to be reflected. It will be reflected for at least 10 – 70 cycles of flashing depending on the user's speed. This reflection will trigger the logic level of the device to low, and then a counter variable within the Arduino program controlling it will increase. Once the white stripe is passed completely and at least 14 more cycles of flashing have passed, the light will no longer be reflected, and the signal will return to a logical high. This process will repeat until a certain amount of time has passed, and then the rpm calculation will be run with the result being sent to the RPi. This will continue again in its own cycle throughout the use of the bike.

D. Steering and External Controls
i) Directional Control
The control system design necessitates some way to convert the steering motion from the user's physical movements on the bike into directional movement and control data that can be used to correspondingly control the character in-game. The component that will serve this purpose must have a reasonable similarity to the steering function of a standard game controller. It must also be able to rotate with the bike at least 90 degrees in both directions for left and right turning. In order to obtain a precise and dynamic measurement of the steering direction, this design will include a potentiometer component that captures degrees of rotational motion from the user and returns that information to the Raspberry Pi to be interpreted as control data. The component selected for this system is a STEMMA 10k Ohm Rotary Potentiometer.

Fig. 13. Steering Component Schematic
This component functions like a standard potentiometer (i.e. variable resistance) where the turning of the dial increases or decreases the amount of current passing through it. The dial has a total rotational range of 270 degrees and will be mounted so that the midpoint at 135 degrees aligns with the center of the bike. Although the user would typically be turning no more than 90 degrees in each direction, the extra room will prevent accidental overturning from breaking the component. This potentiometer component is already contained on a board with connecting wires for each pin. It contains 3 total pins, one for power, one for ground, and the last one for the output signal. The power and ground signals can be directly connected to a 5V and ground pin on the RPi, and the output will go to an analog input GPIO pin. The analog input on the RPi has 10 bits of fidelity, which provides 1024 partitions, similar to the Arduino Nano. Since the user will only be turning 180 degrees total for gameplay (or ⅔ of the total arc), there are only 682 partitions that can be utilized. So, each partition represents 0.26 degrees of turning. This is comparable to the turning fidelity of the accelerometer on a Nintendo Switch controller. The partitions will be split in half, with 341 designated for each direction. The further to each side the user turns, the more partitions are counted by the receiving analog input pin on the RPi. This signal can be translated as a correspondingly increasing or decreasing turn signal in-game. In terms of the physical properties of the translation of bike motion into control data, this design is outlined in detail in the steering portion of the bike system below.

ii) Handlebar Buttons The MarioKart game has several in-game control options

other than the basic steering and acceleration operations. Throwing items at other players and drifting are part of the player’s arsenal, meaning that this design needs some external controls to provide users with the same options as a standard controller. The design will include the attachment of clamping aluminum alloy bike brake levers. The levers will be detachable such that the system remains modular and can be applied to a variety of bike designs. The chosen brake levers are actually meant for E-Bike brakes, so they have a built-in switch. Using a realistic braking system simplifies the drifting and item throwing actions in-game and makes them easy to access while controlling the rest of the bike system. The type of switch used in those E-Bike levers is a "normally open" switch (connected/closed when the button is pressed). More specifically, the buttons will be pressed when the user applies adequate pressure to the levers, causing the circuit to connect. The resulting signal will be sent to the Raspberry Pi as control data for the corresponding button function through digital GPIO pins as shown in the diagram.

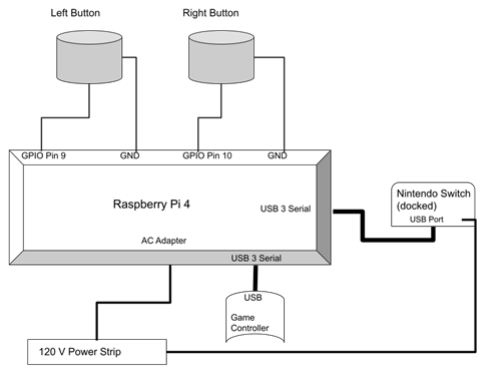
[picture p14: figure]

Fig. 14. Handlebar Buttons Schematic Diagram

The brake levers themselves look like any other standard bike brake lever, except they have two wires coming out of the back. The placement of these brake levers is shown in Fig. 16 on the bike CAD model.

iii) Touchscreen An RPi-compatible 7 inch wide touchscreen tablet

device will be employed as a secondary display. It will be connected through a dedicated ribbon cable directly to the RPi and will serve as the medium for customizable difficulty selection options as well as the method of interaction for the health monitoring system. The connections for this system are outlined in the diagram for the main microcontroller.

E. Game Controller Subsystem
| The game controller will need to be present in order to
preserve menu navigation for the user. The bike parts will only replace a couple of buttons on the controller, meaning that using the console otherwise would be impossible. The game controller is also likely going to be the communication device used to send the inputs to the console. The RPi libraries will send control data that is fed through the game controller and to the console. Therefore a standard console gamepad will be required.

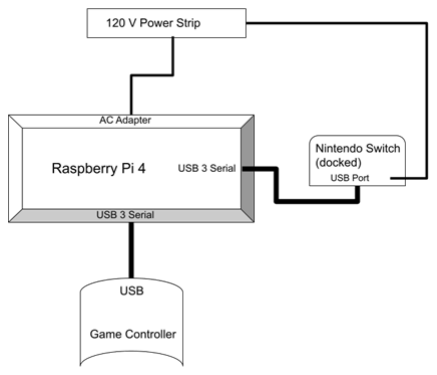
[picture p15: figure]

Fig. 15. Game Controller Schematic

F. Power
Much of the system will be powered through 5V pins on the various microcontrollers. The DC Motor and Magnet resistance circuits, tachometer board, steering component, handlebar buttons, and touch screen will all be powered this way as they require GPIO pin connection as the power source. The microcontrollers for each subsystem will be powered from the USB connections they share with the RPi. The console and monitors will be powered from a standard 120V wall outlet via a power strip located inside the microcontroller box.. The RPi will also be powered this way as it has a dedicated AC adapter on board. There are no batteries or external power circuits necessary for this design.

iv. BIKE SYSTEM

A. Pedals Subsystem
This subsystem must accomplish the task of translating the rotational movement generated by the rider pedaling the bike into a controllable resistance via the magnet or DC motor systems. The main constraint is that very little modification should be made to the bike so that the user may still use their bike on the road.
This subsystem is already taken care of for the magnet bike variant. The magnet/flywheel housing comes with a roller that rests against the rear tire and is also what transfers the resistance from the magnet to the tire.
For the DC motor bike, the team has designed a support that will hold the motor/gearbox assembly. This support will act as the means through which the mechanical motion of the pedals is transferred to the DC motor. The details of this support are explored later in the “Frame Subsystem” section.
B. Steering Subsystem
This subsystem is the other main input that the rider should be able to use to steer in-game. This subsystem must allow for full range of motion of the bike’s handlebars while also translating the rotational movement into game data. It must also be modular and removable for ease of use and easy installation. There are two components to this subsystem: the physical framework that allows the bike itself to turn properly as the user intends and the electronic component that will obtain that physical turning data and convert it into digital data to represent the steering control in-game. The digital component, already covered in the controls subsection, will of course be the potentiometer system. The physical frame component has its own set of constraints that will be met to maintain safety and functionality.
The first constraint of the physical frame will be met via the frame suspending the bike. This frame prevents the front tire from contacting the ground and still allows for full range of motion of the handlebars and will be detailed further in the frame subsystem section. The second constraint requires that the potentiometer be mounted onto the bike and connected to the turn shaft in such a way that the steering motions of the user translate to a corresponding physical manipulation of the encoder rod and thus a steering response by the in-game character. For this, a system of gears including a tall one mounted to the rod of the potentiometer meshed with a thinner one mounted to the turn shaft of the bike will be utilized. The gears will be placed such that the turning at the potentiometer rod is the result of the inverse of the user’s direction, but this will be corrected within the translation code. The potentiometer itself will be held by a clamp placed on the front, static portion of the bike frame that encompasses the turn shaft. This design prevents any manipulation of the potentiometer save for the rotating rod, and it keeps the entire apparatus out of the way of the user. A model of this setup is shown below.

Fig. 16. Prototype CAD Model of the Potentiometer Mounting

C. Frame Subsystem
The frame of the bike must suspend the front and rear wheels off the floor. It must also hold the display that the game will be played on. The frame should be height-adjustable so that various kinds and sizes of bicycle may be attached. The frame should also be foldable or easily disassembled for storage. It should be rigid and wide so that the bike can’t be tipped over from any angle. This is to ensure rider safety.
For the purpose of lifting the bike off the ground, the team has chosen to use a hybrid frame. The back wheel will be suspended by a bike trainer, and the rest of the bike will be held up by a frame designed by the team. The bike trainer serves the dual purpose of lifting the back wheel and providing resistance to it for the magnet bike variant. The chosen bike trainer comes with a manually adjustable magnetic roller, but the adjustment will be automated and controlled by a sub-microcontroller. The rest of the bicycle will be supported by a frame built in-house. The plan is to build it out of one inch steel pipe and connect the pipes using slip-on fittings. The display will be mounted to a vertical pipe at the front of the frame using a VESA pole mount. A concept model of this is shown in the next Figure.

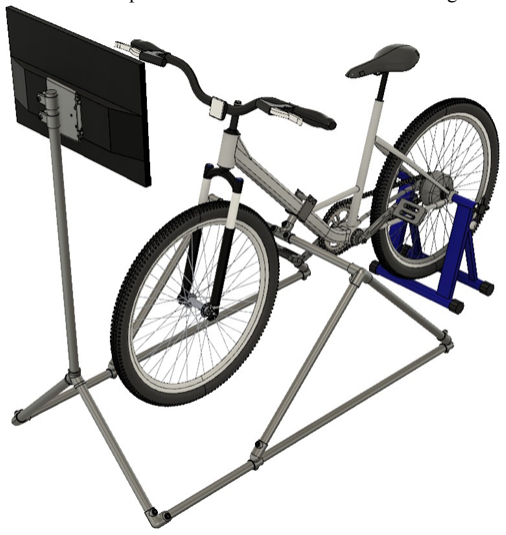
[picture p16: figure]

Fig. 17. Prototype CAD Model of the Bicycle Supporting Frame

The bike trainer attaches using a special pin included in the packaging. This pin replaces the one on the bicycle and allows the bike to be mounted using a single clamp. The bike attaches to the pipe frame via a clamp that is screwed tight. The clamp is intended to allow bikes of various sizes and constructions to be mounted to the frame. It will be angle-adjustable and have a rubber interior for extra grip. The required fittings are a slip-on tee, two three-way 90° slip-on elbows, four 45° slip-on wyes, two 90° slip-on elbows, and a wye connector. The triangles on each side are to prevent the bike from falling forward or backward and side to side. The frame is wide enough to allow full range of motion for the front wheel to steer. The clamp is meant to be mounted in a position on the bike that doesn’t obstruct the motion of the pedals either. The bicycle, bike trainer, pipe fittings, VESA mount, and display are models that the team acquired online. The bicycle was made by user Omkar Narkar on GrabCAD. The bike trainer was made by user Muhammad Furqan on GrabCAD. The display was made by user LeoDJ on GrabCAD. The pipe fittings and VESA mount were acquired from McMaster-Carr’s website.
The motor support mentioned previously is meant to hold the motor/gearbox assembly in a way that allows it to act as a replacement resistance system for the bike trainer stand. The stand comes with a magnetic resistance system that presses against the rear tire. The idea here is that the motor support will mimic the attachment of the existing system. Below is a figure of the proposed motor support.

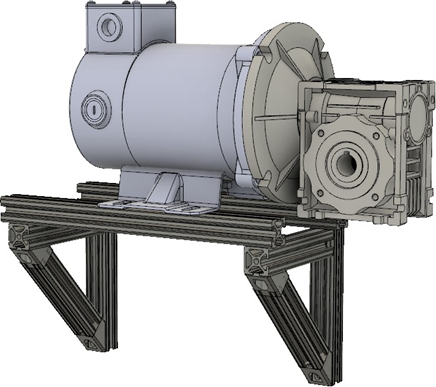
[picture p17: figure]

Fig. 18. Proposed DC Motor/Gearbox Support

The motor will mount to T-slotted framing rails that allow it to slide back and forth. This is needed so that the roller attached to the gearbox can be pressed against various tire sizes. The rails have two 45 degree braces underneath that will serve to support the weight of the motor. They will be attached to the rails using concealed brackets meant for fastening T-slotted framing rails together. This assembly will be attached to two mounting plates on the bike trainer stand. One plate has a vertical slot, and the other a horizontal slot. This allows for angle adjustment. The plates are pictured in Figure 19.

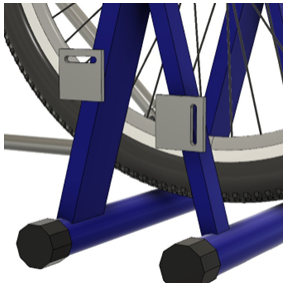
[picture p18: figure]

Fig. 19. Motor Support Mounting Plates

As for the mounting of all of the computing components to the bike frame, a box has been designed. The box houses the Raspberry Pi, two Arduino Nanos, the DC motor/magnet control circuit box, and the power strip. The team decided to put the control circuits in their own boxes due to the high voltage and current being used in the circuit. This smaller box will be velcro taped to the inside of the larger box for ease of removal. The power strip will also be velcro taped to the inner wall of the larger box. The two Nanos will be attached to the floor of the box using M1.6 standoffs and screws. The Raspberry Pi display has been integrated into the lid of the box, sitting perfectly flush. The Raspberry Pi mounts to the underside of the display. The walls of the box are talls enough so that the Raspberry Pi does not come into contact with the other components inside. The box has a large slot at the bottom for all of the cables to feed through. Below is a figure of the lid and the box with estimates of the component placement inside. The box will be attached to the front pole of the frame, just below the monitor, using zip ties or velcro straps. The box will be 3D printed as well.

Fig 20. Computing Control Box

v. HEALTH SYSTEM
A. Calculating Calories: Permanent Magnet Version In this subsystem, the RPi 7” touchscreen will receive the input of the user, then send the data to the Raspberry Pi via a Display Serial Interface (DSI) connector to be calculated internally and displayed on the touchscreen after the user ends the session. For the inputs, the customer must enter their age and weight (lbs), and then press start. The start button is the condition for the function timeDuration() to be enabled. When the user presses the stop button, the amount of time elapsed.
(1) will be calculated in this function and then the value returned will be stored in a variable and passed to calculationMET() to calculate calories (2) with a preset value for the Metabolic Equivalent Task (MET). With the stop button as a condition, the display() function will cause both timeElapsed and calories to be transmitted via the DSI connector to the touchscreen display.

Equation for calculating duration:

(1) timeElapsed = stopTime - startTime

Equation for calculating calories with MET:

(2) calories = T*60*MET*3.5*W

Where the values T = time (hours), MET = Metabolic Equivalent of the chosen task (a preset value), and W = weight (kg, converted from pounds to kilograms).

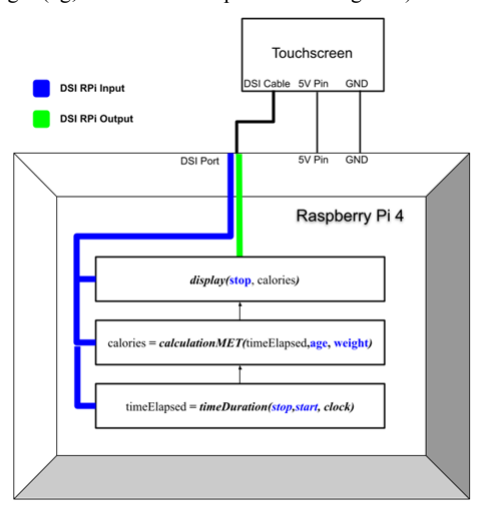
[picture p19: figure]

Fig. 21. Magnet Bike Health System

B. DC Motor Version

This subsystem should read the voltage and current from the Arduino Nano and use the values to calculate power and kilocalories, then output the time elapsed and kilocalories to the 7” display for the customer. The Nano has two analog values for inputs to the DC Motor control. The voltage has a range of 5 volts or 1024 in resolution for Analog to Digital Converter (ADC). The current has 4 volts, or the ADC resolution of 819. The following equation that can be used to convert from the ADC reading:

(1) ADC Resolution/System Voltage = ADC Reading/Measured Voltage

Since the given values would be the system voltage, ADC resolution, and the ADC reading, the measured voltage can be solved for. The same can apply for the current, which is represented by the system voltage of 4 volts.

Example Arduino Code to Demonstrate ADC Reading:

//Defining pin as input
pinMode(A0, INPUT);

//Read analog value of A0 and store in y
int y = analogRead(A0);

//Printing would show the value in ADC resolution Serial.println(y)

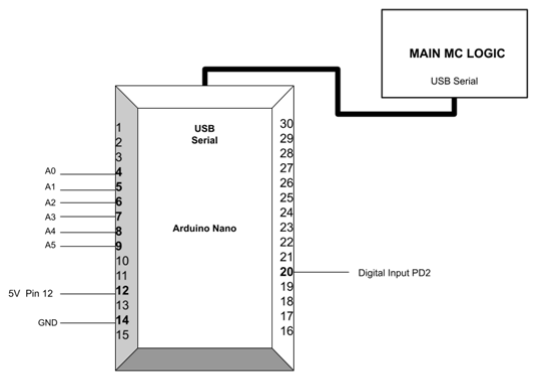
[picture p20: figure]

Fig 22. Motor Bike Health System Data Connections

In order to communicate with the Raspberry Pi (labeled as Main MC LOGIC), the Nano uses a serial USB port. There are libraries that help the Raspberry Pi identify the Nano and access its analog pins. In order to avoid a common issue of having to manually enter the Arduino’s serial device name, there is an available “sketch” project for

Arduino and a library for RPi that has APIs (Application Programming Interface) in C and Python. The link for this solution follows:

https://www.uugear.com/uugear-rpi-arduino-solution/

In addition to the serial USB communication, the user input for start and stop via the DSI of the 7” RPi touchscreen will be input to the system. Once the user presses stop, the RPi function caloriesPower() should use the time computed from a PLL clock, the time elapsed, as well as the current and voltage transmitted from the Arduino Nano serial USB port to compute the power. The code structure flow can be demonstrated from the following equations:

(1) Power = Current * Voltage

The voltage and current will be measured every second in a loop in conjunction with the time elapsed to calculate power.

(2) Kilocalories/Hour = Power * 0.860421

The power will be used as a variable to a second equation to calculate kilocalories per hour.

(3) kcal = Kilocalories/Hour * timeElapsed

The third equation in the function will compute the total kilocalories burned in a session.
Once the user presses the stop button, the arguments to the caloriesPower() function will be the kilocalories and the time elapsed. These variables will be displayed via the DSI connector to the RPi 7” Touchscreen.

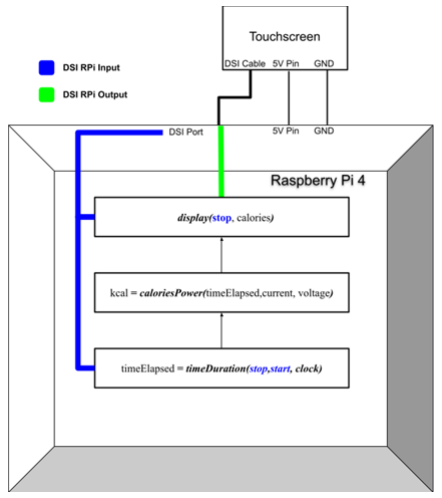
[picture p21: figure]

Fig 23. Motor Bike Health System

Fig 24. Pseudocode

vi. Ethics and Broader Implications
This project aims to avoid any copyright issues by following guidelines provided in Nintendo documentation. Nintendo explicitly states that game ROMs downloaded from the internet are copyright infringements. However, the company has claimed that the use of a backup copy made from an owned copy of the game does not pertain to ROMs downloaded from external sources via the internet. They do not allow selling or distribution of the game from a copied license in this way. The emulated game copy will be used for testing purposes and not for commercial use or exchange. Though there are no legal precedents or trials relating to the individual use of emulators or ROMs, after testing is completed, an officially licensed copy of the game will be used for the final state of the project in order to avoid any legal issues.
The Mario Kart Bike will be designed with consideration of environmental impact. The main housing material will be made of recycled filament for 3D-printers to house buttons. In addition to using environmentally friendly materials, the bike will implement reusing parts such as used bike brake handles to mimic realistic breaking for the player.

The exercise bike will still comply with any regulations or safety standards regarding exercise equipment as we will not be modifying the frame or operational parts in any way that could compromise the integrity or effectiveness. Also, analysis and testing of safe design and operation of the resistive methods will be conducted to prevent physical harm to the user. These safety regulations have determined many design choices. For example, the resistive capacity will be limited to follow existing resistance safety standards on commercial exercise bikes, and the rate of change of resistance will be tuned within the MC interfaces to prevent sudden stops or adjustments that may lead to injury. Also, instead of using a conventional bike that is converted into stationary function, a traditional static exercise bike will be employed and modified to simulate the steering function of a regular bike. This is to allow for greater stability and easier mounting of the motor/magnet systems, again in the interest of preventing injury to the user.
The team conducted an architectural risk analysis on the bike. The consensus is that there are few attack surfaces based on the design. This is evident because there are no wifi or bluetooth connections, although bluetooth is a possibility if it is added in later versions. However, there are serial data connections between the microcontrollers of each subsystem. To mitigate risk, the serial data will be encrypted via code. The team identified the cable linking the controller to the switch as a trust boundary. Unfortunately, the switch data cannot be encrypted. This boundary will be protected with a barrier to house the cord so that the switch data is protected.
There are additional risks to the system’s performance that pertain to user safety. To protect the bike system from being manipulated by the user, components with safety features were selected. For example, the team chose a DC motor with a junction box to house wiring. This decision was made to prevent the user from harm via electric shock.
V. RESULTS AND DISCUSSION
A) Pedals Subsystem:
The purpose of this subsystem is to translate the rotational movement of the bike's pedals to the DC motor resistance system. The main constraint is that no major modification can be made to the bike so that it may still be rideable on the road. The design outlook has changed since design phase 2 was written. It has evolved into an easier method, while still maintaining the specs and constraints. To test this subsystem, a rider pedaled the bike and it was demonstrated that the bike tire roller was able to transfer the motion through a flexible shaft to the DC motor sitting on the floor. No modifications were made to the bike besides adding a couple of bolts to the rear axle so that it may sit in the bike trainer more securely.
Various riders have indicated that having the pedals attached to the DC motor does not hinder gameplay, but it does add a noticeable amount of resistance even when the motor is not being braked. Therefore, it can be concluded that the subsystem is successful and no further improvements are necessary for base functionality of the subsystem.

The following video demonstrates the experiment: https://drive.google.com/file/d/1FQCbuubpCnskCKTeCOQMqnzUGAGgylcD/view?usp=sharing (https://drive.google.com/file/d/1FQCbuubpCnskCKTeCOQMqnzUGAGgylcD/view?usp=sharing)

B) Steering Subsystem:
The purpose of this subsystem is to transfer the rotational movement of the bike's handlebars to a potentiometer that will convert it into game data. The constraints are that it must be modular and removable when not in use. The design has changed slightly since phase 2, but the basic idea is the same. Two gears translate the motion to the potentiometer, and the whole assembly is removable via screws. Although, the gear attached to the bike doesn't have to be removed as it doesn't hinder normal operation of the handlebars.
To test this subsystem, a rider turned the handlebars 180 degrees at varying speeds and forces. The gears can turn further than 180, but no sane rider would need to do that in-game. It has been found that the steering control could be tuned to provide more steering per degree of rotation, but that will be fixed in software. As far as the physical subsystem goes, the design is successful and no changes need to be made for base functionality.

The following video shows a demonstration of the experiment:
https://drive.google.com/file/d/1FfzsU2vSYcDkufuFrZ7AIU6jiKNoKl8x/view?usp=sharing (https://drive.google.com/file/d/1FfzsU2vSYcDkufuFrZ7AIU6jiKNoKl8x/view?usp=sharing)
C) Frame Subsystem:
The purpose of this subsystem is to suspend the bike and the rider off the ground. This is to ensure that the front and rear wheels can move freely to serve functionality for other subsystems. It also must hold the game's display for an arcade-style gaming experience. The constraints are that the frame must be height-adjustable, foldable and/or easily disassembled, and rigid/wide enough to support any rider and prevent tipping over.
The design of the frame was not changed from phase 2 except for the way the DC motor is mounted. It is no longer secured to the bike frame. It instead sits on the floor with rubber feet. The rest of the frame was built to spec. To test the strength of the frame, a rider stood on the bike, leaned both ways, and pedaled. The monitor mount was also nudged to test for wobble and stability. The results were good. The frame did not exhibit any significant wobble. The monitor can be wobbled by hand, but it does not move while the rider is pedaling. The bike is held off the ground securely. The only way that the constraints were broken is that the front wheel had to be removed. However, it is easily reattached with two bolts and it even makes steering easier and more fluid to have no front wheel.

The following video shows the experiment: https://drive.google.com/file/d/1FirlIeNljJ6o62IekmWVKg16TLf-UYEZ/view?usp=sharing (https://drive.google.com/file/d/1FirlIeNljJ6o62IekmWVKg16TLf-UYEZ/view?usp=sharing)

D) DC Motor Resistance Subsystem:
The purpose of the DC motor is to provide dynamic resistance to the pedals of the bike and therefore the rider. The main constraint is that the system must be self-contained and unable to harm anyone using it. This DC motor outputs high voltage and current so this is imperative. Several precautions have been made to prevent shock.
The purpose of the MOSFET is to provide a way to control the braking of the motor. However, through extensive testing, it has been found that the selected MOSFET will not work for two reasons. One is that the transistor is rated to dissipate 160W while switching. It has been found that the motor can generate up to 260V and 1.2A, which obviously leads to a power much higher than
160. The second reason is that this is a typical n-channel MOSFET, meaning its intended use is as an on/off switching device. By operating it in the linear region, we are introducing a catastrophic amount of internal heat. This has led to two of the MOSFETs internally shorting and becoming unusable. Additionally, the chips meant to measure the current and voltage generated at all times are not functional. In phase 2, it was thought that the chips could be powered by the DC motor. However, that is not the case. The op amps and hall sensor need a dedicated power source to be functional. Therefore, the measurements conducted in the experiments below were done by a DMM. The solution that has been implemented (for now) is to instead put a relay across the motor leads. This is not a permanent solution, but it is what we used for the experimentation that will be mentioned below. The relay serves the same purpose, which is that we can control the high power motor with a low power device (the Arduino). However, the resistance is not dynamic. Because it is a relay, it can ONLY be treated as a switching device. We have implemented a program that randomly turns the relay on for 30 ms, which creates a noticeable jump in resistance for a brief moment. These jumps in resistance happens randomly every 15-45 seconds. This adds an element of exercise on top of what is already present. Driving the motor in an open state already leads to a considerable amount of resistance, along with the random jolts.
Again, the above solution with the relay is only temporary. However, some experimentation has been done using the temporary system. To test the performance of the motor, we had a rider run 4 races. In 3 of them, we measured the voltage generated by the motor. In the fourth, we measured the current generated. The reason we only did one trial of current measurement is because the motor is open for the majority of the race due to the relay. That means that theoretically, zero current will be generated. We did one trial to prove that. For the voltage trials, it was found that an average of 140-160 Volts is steadily generated throughout the race. Further, because "zero" current is being generated, that means a very small amount of power was generated (microWatts). The results have been plotted below.

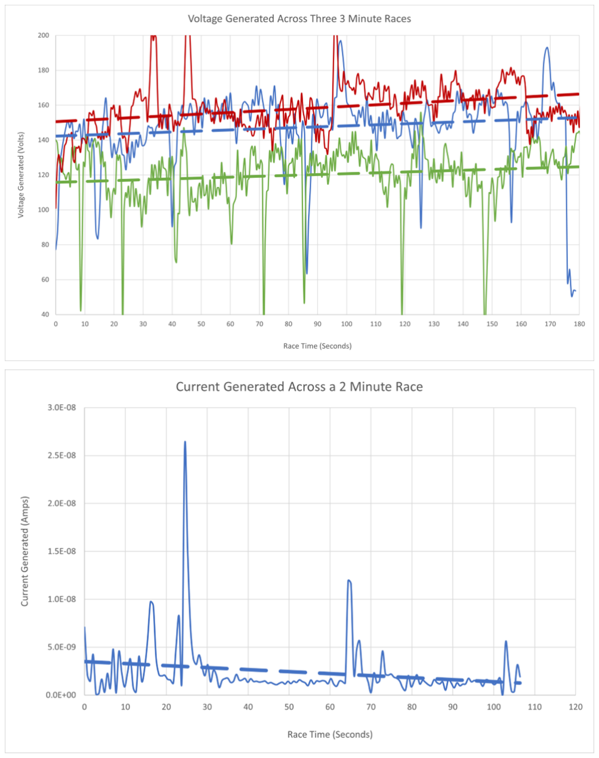
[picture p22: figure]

Fig 25. Voltage and Current Generated from DC Motor

The dashed lines represent the average across the data spread. The voltage graph has 3 trials on one plot, each taking about 3 minutes. The rider pedaled at various speeds in each trial, which is evident by the slight difference in the average voltage generated when comparing the three. The large dips in the lines were caused by the random jolts from the relay being turned on. The reason the voltage dips so much is because when the jolt happens, the RPM of the motor drops significantly, leading to less voltage generated. With this, we would consider the results of the experiment successful. The relay worked as intended and added a considerable amount of exercise to the riding experience. It has also been shown that a considerable amount of voltage can be extracted from the system.
In the future, the relay will be replaced with a linear mode MOSFET with high power dissipation. A linear mode transistor is meant to operate in the linear region, which means the high internal heat will be reduced. Along with higher power dissipation, this should lead to a system that functions as originally intended. Additionally, the op amps and hall sensor will be given a dedicated power source and their functionality will be tested later. Once those improvements have been made, we will run the same trials again and compare the results.
A video was not recorded for this experiment because the operation of the resistance system has been showcased in the video for the Pedals Subsystem.
E) Steering Subsystem
The steering subsystem consists of a 10k Ohm potentiometer and a 12-bit ADC chip with an onboard gain amplifier. The potentiometer is connected to the 5V power and ground of the RPI, and its output is fed into the first analog channel of the ADC. The ADC is also powered by the RPI, and its digital output is returned via I2C. Steering is mechanically translated from the user turning the handlebars by a 1 to 1 gear ratio with one piece around the turn shaft of the bike and the other around the knob of the potentiometer. The potentiometer is mounted such that the middle position of the range is facing directly forwards away from the user of the bike. It has 135 degrees of physical rotation available in each direction.
It was originally expected that the user could only practically operate the handlebars in a range of 90 degrees left or right of the center point. This limited our range of the potentiometer to only 180 degrees out of 270 total degrees available or 2/3 of the base range. The ADC chip measuring 12 bits gives 4096 partitions of measurement possible. Over a range of 5 volts, this works out to be 0.0012207 Volts per partition. Because we are only using 2/3 of the voltage range for controls, we expected about 2730 partitions or 3.333 Volts of practical range. The Nintendo Switch controller analog signal for horizontal movement only scales up to 4096 partitions as well, meaning we still planned to have 2/3 of the range of standard controller steering. Given the already high precision of the controller, we had concluded that the output of the ADC should be directly mapped to steering data from the switch, and that the difference in range would be insignificant for standard play. The physical design of the gear system should ideally result in the same turning distance and speed as turning the potentiometer by hand via the knob.
The steering implementation ended up being relatively close to the specifications. It has the highest priority of all control signals because of its necessary precision and responsiveness. In terms of the range of fidelity the user has when playing the game, the 180 degree range allows access to the 500th to the 3500th partition in the range. However, the 12-bit ADC chip has peculiar gain options that prevent exactly 5 volts from being utilized as the range limiter. The closest choices were either 4.096 V at a gain of 1 or 6.144 V at a gain of 2/3. Selecting the 2/3 gain option allowed us to use the full range, but the value of the voltage affected by each partition changed, so the voltage range the user has access to practically in the 180 degree range is 0.75 V to 5.25 V. Fortunately, the potentiometer and the RPi have no issue with this difference in range and function just as well as predicted. The steering is mapped one-to-one from the returned digital bit value to the horizontal analog left stick input (steering stick in MarioKart). This was possible because, coincidentally, the analog stick in a Nintendo Switch controller also has 12 bits of fidelity for the horizontal position. The slight loss in range on either end of the steering has not proven to be significant to performance due to the gradual steering process in-game. Functionally, this subsystem works exactly as planned. Subjectively, a different approach to the mapping might be beneficial in the future. While pushing an analog stick all the way to one side is relatively easy and makes sense for a hard turn, turning bike handlebars all the way to one side while pedaling has proven to be awkward and difficult to adjust to while playing. An exponential form of mapping, where the partition value being mapped is increased faster as the user turns, should solve this problem. One other issue has appeared recently with the connection between the ADC and the RPi where the I2C occasionally loses connection, but this is most likely due to the connection being between jumper wire headers and not permanently soldered in place.

Video Testing:
https://drive.google.com/file/d/1hmFfyGo91mm45ISRFt6g9mDjMVWMiVlL/view?usp=sharing (https://drive.google.com/file/d/1hmFfyGo91mm45ISRFt6g9mDjMVWMiVlL/view?usp=sharing)

Once a better mapping for the steering is developed, it would be beneficial to test it and compare to the current mapping to see if the quality can be improved subjectively. If there could be a basic exponential function set up to correctly increase the rate of steering as the user turns further to each direction, we can tune it after repeated play-testing. Additionally, another test with different ADC gain settings selected might be beneficial depending on the result of the new mapping design. It could help add just a bit more fidelity to the turning itself.
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

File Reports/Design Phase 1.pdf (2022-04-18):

# ECE 4961- Group 2 - MarioKart Bike Design Phase 1

Reed Hester, Chase Griffin, Leah Faulkner ECE Students, Tennessee Technological University Cookeville, TN, United States of America lrhester42@tntech.edu
cagriffin42@tntech.edu
lmfaulkner42@tntech.edu

Abstract --- This report dives deeper into the high-level design of the MarioKart bike. A block diagram of the system with descriptions for each block is given. Analysis, testing, and broader implications are also explored.

Keywords --- Capstone Design, gaming, emulation, exercise, sensors, electromagnetics, engineering

I. INTRODUCTION
The Mario Kart exercise bike project is the result of an idea to bring physical activity together with the excitement of the racing video game experience. The objective with this idea is to design and develop a practical way to exercise using the traditional resistive elements of an exercise bike while simultaneously controlling a player in a game of Mario Kart in a simple-to-use, responsive, and enjoyable way. By using the bike as a direct controller, the player will be able to play as fluidly as they could with a standard controller with the added benefit of physical activity. Ideally, the bike will serve as a tool to assist in promoting a healthy lifestyle in an entertaining way.
To achieve this goal, the use of several external control systems combined with the inputs from a standard game controller will be employed. Microcontrollers with code interfaces set up to specifically target the operations for each subsystem of the controls will be utilized as well. These powered subsystems will consist of an adjustable resistance method, a pedalling speed sensing system, an encoded steering system, and an actual standard game controller. The resistance method will vary between two experimental versions of the bike. One method will consist of a magnetic resistance system involving a linear actuator that can incrementally increase or decrease the physical distance of a magnet from the bike wheel, thus creating dynamic resistance based on said distance. The other method of resistance is to use a DC motor connected to a MOSFET that allows the motor to be shorted on command, which creates resistive force when the motor is being spun. The pedalling sensor system will involve a tachometer sensor that measures the speed of the revolving pedals and uses that information to control the acceleration of the player’s vehicle. The steering mechanism will govern a rotary encoder which will be used to interpret directional controls. Finally, in order to simplify menu navigation and other game interactions, a standard game controller will be included as well with the traditional button layouts and usage. Each of the sub-microcontrollers in these systems will be routed into a main microcontroller or RaspberryPi device that interprets the received data into usable control information that is
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

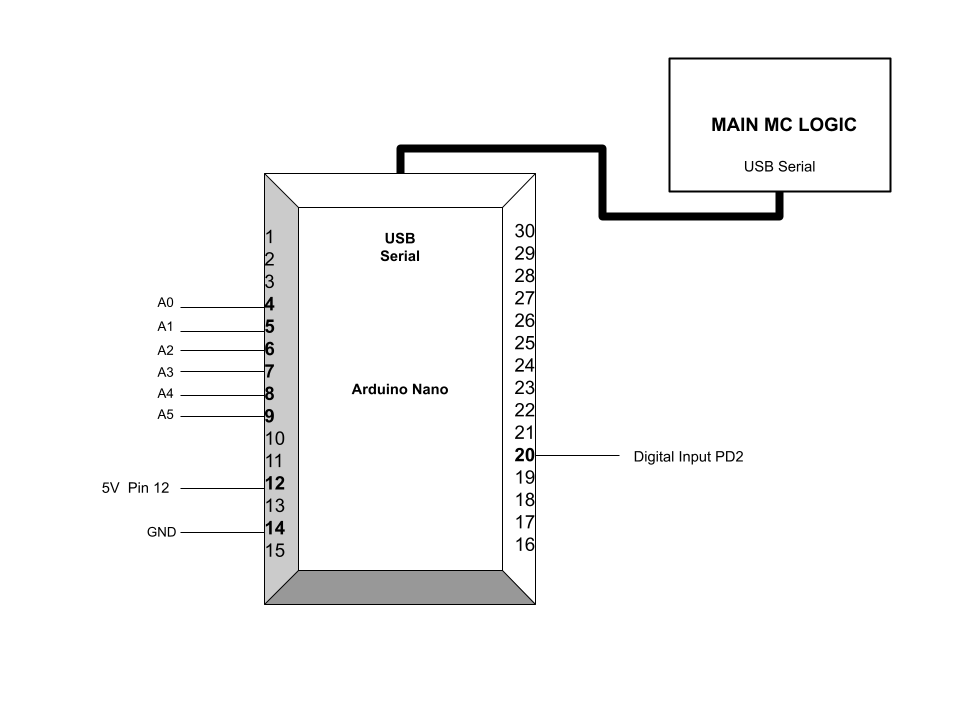
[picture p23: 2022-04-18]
Project_Documentation/Design Artifacts/Calorie Nano Circuit.png

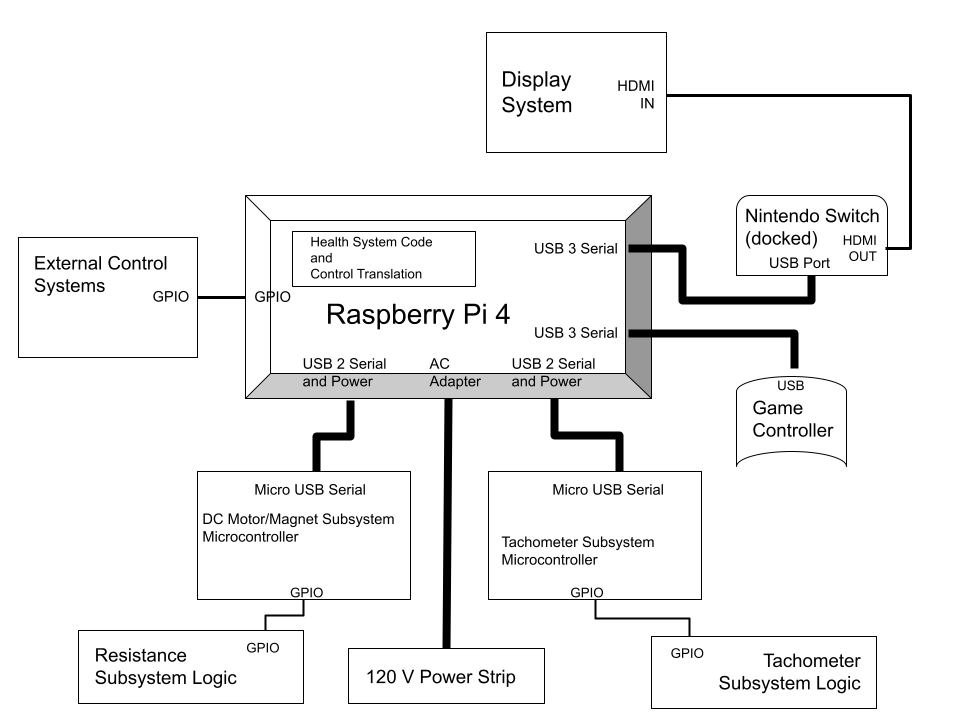
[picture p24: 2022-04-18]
ProjectDocumentation/Design Artifacts/Conceptual Schematic.png

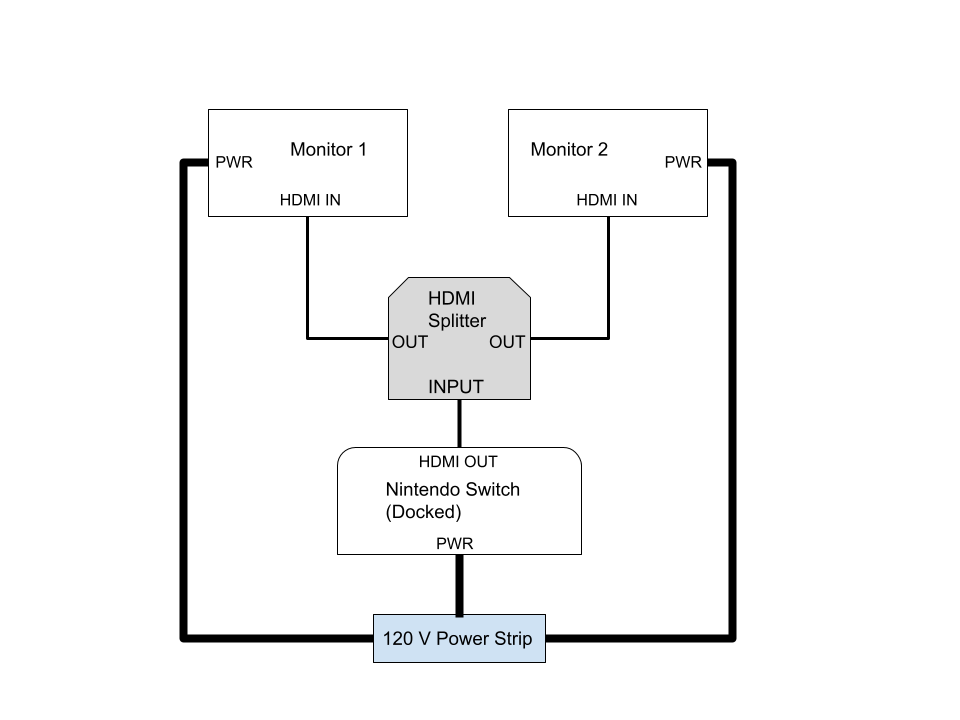
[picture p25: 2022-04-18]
Project_Documentation/Design Artifacts/Display schematic.png

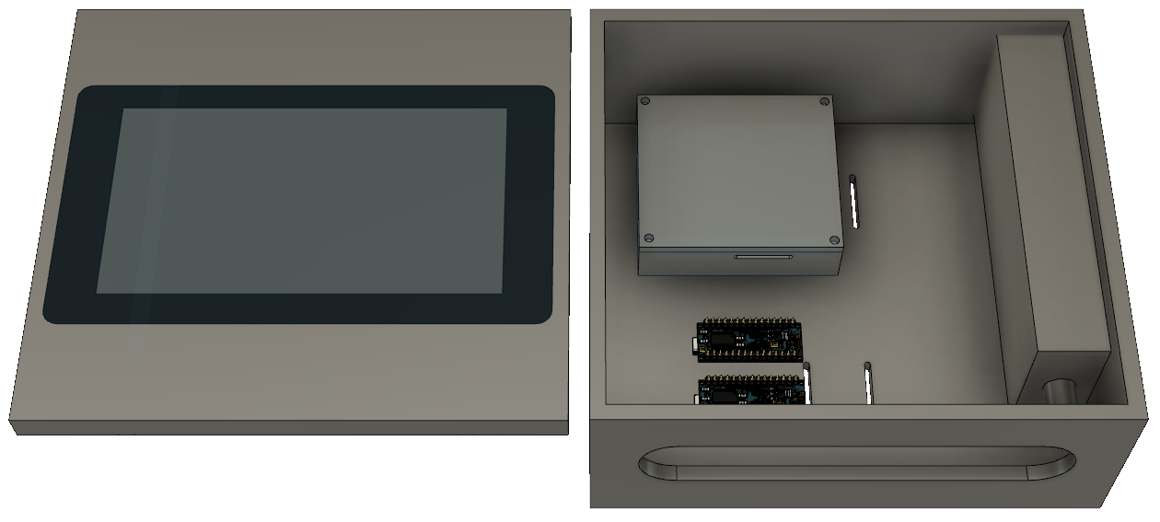
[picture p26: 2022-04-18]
ProjectDocumentation/Design Artifacts/board box.png

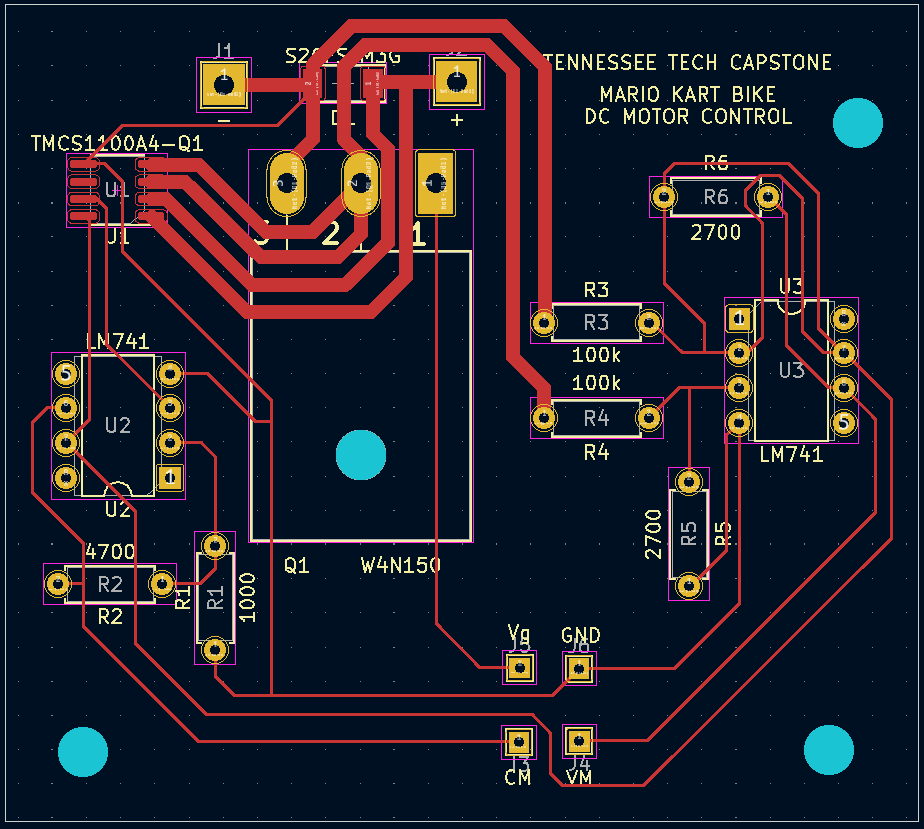
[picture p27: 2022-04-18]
ProjectDocumentation/Design Artifacts/PCB schematic.png

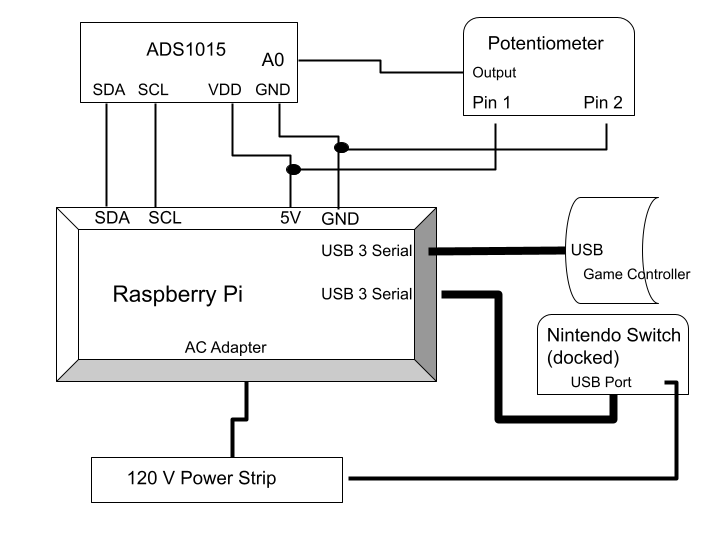
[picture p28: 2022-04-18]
ProjectDocumentation/Design Artifacts/Pot and ADC schematic.png

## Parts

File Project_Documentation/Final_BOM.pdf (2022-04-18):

Number Part | Description | Manufacturer | # | Product Link | Cost per Item | Total Cost
A000005 | Arduino Nano | Arduino | 4 | https://store-usa.arduino. | $20.70 | $82.80
cc/products/arduino-nan
o?selectedStore=us (https://store-usa.arduino.cc/products/arduino-nano?selectedStore=us)

RP4B4GB

Raspberry Pi 4
Model B - 4 GB
RAM

Raspberry Pi 2

https://vilros.com/produc
ts/raspberry-pi-4-4gb-ra
m?src=raspberrypi (https://vilros.com/products/raspberry-pi-4-4gb-ram?src=raspberrypi)

$55.00 $110.00

SC0025

Official
Raspberry Pi 7"
Touchscreen
LCD Display

Raspberry Pi 2

https://vilros.com/produc
ts/raspberry-pi-7-touchsc
reen-lcd-display?src=ras
pberrypi (https://vilros.com/products/raspberry-pi-7-touchscreen-lcd-display?src=raspberrypi)
$74.95 | $149.90
TMCS110 0A4QDR Q1 | Automotive hall effect sensor | Texas Instruments | 3 | https://www.mouser.com/ProductDetail/Texas-Instruments/TMCS1100A4QDRQ1?qs=QN EnbhJQKvbjO1r%252 BMdmvKQ%3D%3D (https://www.mouser.com/ProductDetail/Texas-Instruments/TMCS1100A4QDRQ1?qs=QNEnbhJQKvbjO1r%252BMdmvKQ%3D%3D) | $3.76 | $11.28
S2GFS M3G | Power Diode | Taiwan Semiconductor | 3 | https://www.digikey.com/en/products/detail/ta iwan-semiconductor-co rporation/S2GFS-M3G /12806672 (https://www.digikey.com/en/products/detail/taiwan-semiconductor-corporation/S2GFS-M3G/12806672) | $4.34 | $13.02
MTPM-P3 3-1M18 | DC Motor | IronHorse | 1 | https://www.automationdirect.com/adc/shopping/catalog/motors/dc_motors_(up_to_2hp)/g eneral_purpose/mtpm-p33-1m18 (https://www.automationdirect.com/adc/shopping/catalog/motors/dc_motors_(up_to_2hp)/general_purpose/mtpm-p33-1m18) | $186 | $186
WGA-40 M-020-H1 | Gearbox | IronHorse | 1 | https://www.automationdirect.com/adc/shopping/catalog/power_transmission_(mechanical)/ general_purpose_alumi num_worm_gearboxes /wga-40m-020-h1 (https://www.automationdirect.com/adc/shopping/catalog/power_transmission_(mechanical)/general_purpose_aluminum_worm_gearboxes/wga-40m-020-h1) | $140 | $140
KY-032 | Tachometer | Keyes | 3 | https://www.amazon.com/Electronics-Infrared -Obstacle-Avoidance-Arduino/dp/B0786B8J 92 (https://www.amazon.com/Electronics-Infrared-Obstacle-Avoidance-Arduino/dp/B0786B8J92) | $3 | $9
4493 | Potentiometer | STEMMA | 2 | https://www.adafruit.com/product/4493#descri ption (https://www.adafruit.com/product/4493#description) | $3.95 | $7.90
N/A | Motor Controller PCB | JLCPCB | 5 | https://cart.jlcpcb.com/quote (https://cart.jlcpcb.com/quote) | $2.00 | $2.00

B07DR9S 5C9 | E-Bike Brake Levers with Switches | Dioche | 2 | https://www.amazon.com/Brakes-Durable-Bic ycle-Electric-Replace ment/dp/B07DR9S5C9 /ref=sr_1_2?keywords =e-bike+brake+lever& qid=1643332384&sr=8 -2 (https://www.amazon.com/Brakes-Durable-Bicycle-Electric-Replacement/dp/B07DR9S5C9) | $21.99 | $43.98
4936T345 | 1" OD galvanized steel framing rail (10 feet) | McMaster-Carr | 1 | https://www.mcmaster.com/4936T101-4936T345/ (https://www.mcmaster.com/4936T101-4936T345/) | $85.09 | $85.09
4936T307 | 1" OD galvanized steel framing rail (5 feet) | McMaster-Carr | 1 | https://www.mcmaster.com/4936T101-4936T307/ (https://www.mcmaster.com/4936T101-4936T307/) | $42.54 | $42.54
4698T31 | 90 degree elbow connector for 1" rail | McMaster-Carr | 2 | https://www.mcmaster.com/4698T31/ (https://www.mcmaster.com/4698T31/) | $10.52 | $21.04
4698T96 | Adjustable angle wye connector for 1" rail | McMaster-Carr | 4 | https://www.mcmaster.com/4698T96/ (https://www.mcmaster.com/4698T96/) | $18.16 | $72.64
4698T86 | Adjustable angle cross connector for 1" rail | McMaster-Carr | 1 | https://www.mcmaster.com/4698T86/ (https://www.mcmaster.com/4698T86/) | $26.92 | $26.92
4698T73 | Adjustable angle elbow connector for 1" rail | McMaster-Carr | 2 | https://www.mcmaster.com/4698T73/ (https://www.mcmaster.com/4698T73/) | $22.84 | $45.68

NB-SC6-B
S12

Tie down
cradle for 1"
tubing (set of
6)

BIKEGEAR 1

https://www.amazon.co
m/BIKEGEAR-Replac
ement-Accessory-Hitc
hing-Carriers/dp/B08D
FDCH5J/ref=sr_1_1_s
spa?crid=O1DJ872W4
DS9&keywords=bike+
rack+cradle&qid=1643
338235&sprefix=bike+
rack+cradle%2Caps%2
C132&sr=8-1-spons&
psc=1&spLa=ZW5jcnl
wdGVkUXVhbGlma
WVyPUEzNFlJM01R
Wk9LUzRUJmVuY3J
5cHRlZElkPUEwMzQ
1ODM3MkhURFVY
WVBIT0hYVSZlbmN
yeXB0ZWRBZElkPU
EwNDY0ODIxMUNU
MklRODZBSVFFUiZ
3aWRnZXROYW1lP
XNwX2F0ZiZhY3Rpb (https://www.amazon.com/BIKEGEAR-Replacement-Accessory-Hitching-Carriers/dp/B08DFDCH5J)

$49.50 $49.50

| | | | 249Y2xpY2tSZWRpc mVjdCZkb05vdExvZ0 NsaWNrPXRydWU= (https://www.amazon.com/BIKEGEAR-Replacement-Accessory-Hitching-Carriers/dp/B08DFDCH5J)
72457 | Zefal "Cristophe" Mountain Bicycle Half Toe Clip S/M (CHOOSE S/M SIZE) | Zefal | 1 | https://www.amazon.com/Zefal-Cristophe-Mountain-Bicycle-Clips/dp/B000AO9K9S/ref=sr_1_23?keywords=toe %2Bcages%2Bfor%2B bike%2Bpedals&qid=1 642108542&s=sportin g-goods&sprefix=toe% 2Bcage%2Csporting% 2C124&sr=1-23&th=1 &psc=1 (https://www.amazon.com/Zefal-Cristophe-Mountain-Bicycle-Clips/dp/B000AO9K9S?s=sporting-goods) | $11.90 | $11.90
854175117 4 | Universal Monitor Pole Mount Bracket with VESA 75/100 | Loutytuo | 1 | https://www.amazon.com/Loutytuo-Universal-Punching-Adjustable-Diameter/dp/B07R7SC4B8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 le%2Bmount%2Coffic e-products%2C81&sr= 1-3&th=1 (https://www.amazon.com/Loutytuo-Universal-Punching-Adjustable-Diameter/dp/B07R7SC4B8?s=office-products) | $37.89 | $37.89

B089NKP
W39

Bike

Trainer
Stand Indoor
Riding Steel
Bicycle
Exercise Stand
with Noise
Reduction
Wheel
Magnetic
Stationary
Stand fits for
26-28inch,
700C Wheel

Unisky

1

https://www.amazon.co
m/Exercise-Magnetic- (https://www.amazon.com/Exercise-Magnetic-Training-Stationery-Mountain/dp/B0876XCFC3?s=sporting-goods) Training-Stationery-M

ountain/dp/B0876XCF
C3/ref=sr_1_2_sspa?cr
id=3OLXTK8CJPKB1
&keywords=bike%2Bt
rainer&qid=16420927
62&s=sporting-goods
&sprefix=bike%2Btrai
ner%2Csporting%2C1
02&sr=1-2-spons&spL
a=ZW5jcnlwdGVkUX
VhbGlmaWVyPUExM
FcyN1UyTElWMFBH
JmVuY3J5cHRlZElkP
UEwNDU1NTk4M0R
IMDJBUzQ4UkdXViZ
lbmNyeXB0ZWRBZE
lkPUEwOTQ1Mjk1M
0VJNDdBSk0xUzM5
RSZ3aWRnZXROYW
1lPXNwX2F0ZiZhY3
Rpb249Y2xpY2tSZW
RpcmVjdCZkb05vdEx
vZ0NsaWNrPXRydW
U&th=1 (https://www.amazon.com/Exercise-Magnetic-Training-Stationery-Mountain/dp/B0876XCFC3?s=sporting-goods)

$89.99 $89.99

B092VJX
GJ6

HDMI
Splitter, 1 in 2
Out 4K HDMI

ZI YOUREN

1

https://www.amazon.co
m/Splitter-Monitors-D
uplicate-Amplifier-Dis
plays/dp/B092VJXGJ6 (https://www.amazon.com/Splitter-Monitors-Duplicate-Amplifier-Displays/dp/B092VJXGJ6?hvadid=507563721518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)

$10.99 $10.99

| Splitter Display Duplicate/Mirr or, 1x2 HDMI Splitter One Input to Two Outputs for Full HD 4K@30HZ 1080P 3D Splitter (1 Source to 2 Displays) | | | /ref=asc_df_B092VJX GJ6/?tag=hyprod-20&l inkCode=df0&hvadid= 507563721518&hvpos =&hvnetw=g&hvrand =12334949305384762 110&hvpone=&hvptw o=&hvqmt=&hvdev=c &hvdvcmdl=&hvlocint =&hvlocphy=1025954 &hvtargid=pla-134499 8815656&psc=1 (https://www.amazon.com/Splitter-Monitors-Duplicate-Amplifier-Displays/dp/B092VJXGJ6?hvadid=507563721518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)
BO81ZQK XN4 | Power Strip with 2 Outlets and 3 USBs | One Beat | 1 | Amazon.com: Power Strip with USB - 2 Outlets 3 USB Charging Ports(3.1A, 15W), Desktop Charging Station with 5 ft Braided Extension Cord, Flat Plug Travel Power Strip for Cruise, Home Office, ETL Listed : Electronics (https://www.amazon.com/Outlets-Charging-Desktop-Station-Extension/dp/B081ZQKXN4?s=electronics) | $12.29 | $12.29
QXAD007 2 | M1.6x2.5mm( OD)x4mm(L), 30 Pcs | Antrader | 1 | https://www.amazon.com/Antrader-Female-Kn urled-Embedment-Ass ortment/dp/B07TTQX VQH/ref=sr_1_4?crid= 198A91X2M0809&ke ywords=m1.6%2Bstan doff&qid=1643760584 &sprefix=m1.6%2Bsta ndoff%2Caps%2C466 &sr=8-4&th=1 (https://www.amazon.com/Antrader-Female-Knurled-Embedment-Assortment/dp/B07TTQXVQH) | $5.99 | $5.99
20181113 | OEM Standoff Bolt Stainless Steel M1.6 | Yufu | 16 | https://www.alibaba.com/product-detail/Yufu-OEM-Standoff-Bolt-Stainless-Steel_60827022836.html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 W7 (https://www.alibaba.com/product-detail/Yufu-OEM-Standoff-Bolt-Stainless-Steel_60827022836.html) | $0.01 | $0.16
NJASD63 2891 | Caution Electrical Safety Hazard Sticker Pack of 3 | D Sticky Company | 1 | https://www.amazon.com/Caution-Electrical-Safety-Hazard-Sticker/dp/B085G4VS7F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 (https://www.amazon.com/Caution-Electrical-Safety-Hazard-Sticker/dp/B085G4VS7F) | $6.99 | $6.99
47065T80 1 | T-Slotted Framing | McMaster-Carr | 2 | https://www.mcmaster.com/47065T801/ (https://www.mcmaster.com/47065T801/) | $5.53 | $11.06

| Single Four Slot Rail, Silver, 1" High x 1" Wide, Solid INPUT 7 INCH LENGTH
3136N147 | T-Slotted Framing Screw on Bumper for 1" High Single Rail | McMaster-Carr | 4 | https://www.mcmaster.com/3136N147/ (https://www.mcmaster.com/3136N147/) | $4.25 | $17.00
3787K13 | Flexible Shaft with Female x Female Fittings 1/2 Feet Overall Length, 1/4" OD | McMaster-Carr | 1 | https://www.mcmaster.com/3787K13/ (https://www.mcmaster.com/3787K13/) | $84.81 | $84.81
3084K66 | Machinable-B ore Clamping Shaft Coupling Steel, for 5/8" x 0.625"-0.235" Keyed Shaft Diameter | McMaster-Carr | 1 | https://www.mcmaster.com/3084K66/ (https://www.mcmaster.com/3084K66/) | $54.72 | $54.72
3084K91 | Machinable-B ore Clamping Shaft Coupling Steel, for 10 mm x 10.000 mm-6.000 mm Round Shaft Diameter | McMaster-Carr | 1 | https://www.mcmaster.com/3084K91/ (https://www.mcmaster.com/3084K91/) | $43.03 | $43.03
1555T121 | Linear Motion Shaft 1060 Carbon Steel, 1/4" Diameter, 6" Long | McMaster-Carr | 1 | https://www.mcmaster.com/1555T121/ (https://www.mcmaster.com/1555T121/) | $9.07 | $9.07
MTA-BAS E-W56 | STABLE motor base, for use with | Automation Direct | 1 | https://www.automationdirect.com/adc/shopping/catalog/motors/motor_bases_(for_nema_motors)/mta-base-w56 (https://www.automationdirect.com/adc/shopping/catalog/motors/motor_bases_(for_nema_motors)/mta-base-w56) | $12.25 | $12.25

| 56 frame motors
47065T23 3 | T-Slotted Framing Drop-in Nut with Stud, 1/4"-20 Thread Size | McMaster-Carr | 4 | https://www.mcmaster.com/47065T233/ (https://www.mcmaster.com/47065T233/) | $1.86 | $7.44
1954 | Machine Screw: M1.6, 3mm Length, Phillips (6-pack) | Generic | 3 | https://www.pololu.com/product/1954/specs (https://www.pololu.com/product/1954/specs) | $1.99 | $5.79
ASHATAy 53iq2gz9w | 20Pcs Threaded Insert, Self Tapping Slotted Screw Thread Insert, Stainless Steel, Knife Thread, M3 x 0.5 Inner Thread, M5 x 0.5 Outer Thread, 6mm | ASHATA | 1 | https://www.amazon.com/Stainless-SUS303-Tapping-Slotted-Thread/dp/B07X9JQ79Q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 readed+insert+for+plas tic%2Caps%2C138&sr =8-13 (https://www.amazon.com/Stainless-SUS303-Tapping-Slotted-Thread/dp/B07X9JQ79Q) | $10.19 | $10.19
GDA6015 | 2-Pack 60mm x 15mm USB Fan 5V Brushless DC Cooling Fans | GDSTIME | 1 | Amazon.com: GDSTIME 2-Pack 60mm x 15mm USB Fan 5V Brushless DC Cooling Fans for PC Computer Case Cooler Raspberry Pi Radiator Ventilation : Electronics (https://www.amazon.com/gp/product/B08SQDF6F3/ref=ppx_yo_dt_b_asin_title_o00_s00?ie=UTF8&th=1) | $14.26 | $14.26
ADS1015 | 12-Bit ADC -4 Channel with Programmable Gain Amplifier | Adafruit | 1 | https://www.adafruit.com/product/1083 (https://www.adafruit.com/product/1083) | $9.95 | $9.95
B08SQDF 6F3 | 2-Pack 60mm x 15mm USB Fan 5V | GDSTIME | 1 | https://www.amazon.com/gp/product/B08SQDF6F3/ref=ppx_yo_dt_b_asin_title_o00_s00?ie=UTF8&th=1 (https://www.amazon.com/gp/product/B08SQDF6F3/ref=ppx_yo_dt_b_asin_title_o00_s00?ie=UTF8&th=1) | $12.99 | $12.99
Total Quantity of Parts: | | | 84 | Total Cost: | | $1,568.05

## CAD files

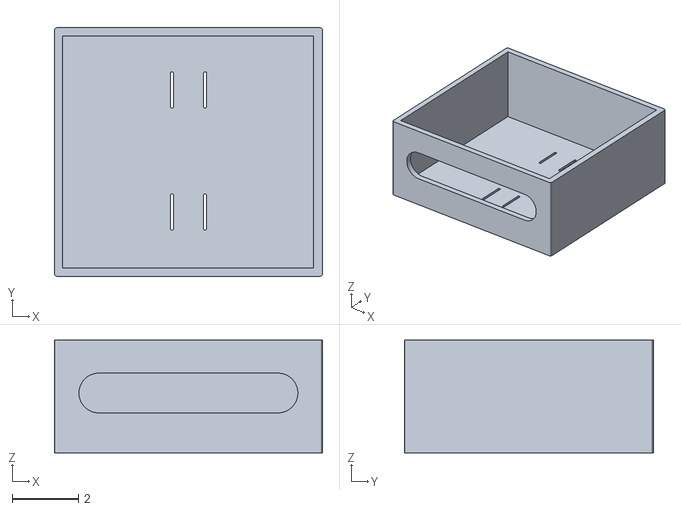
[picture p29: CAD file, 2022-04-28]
Project_Documentation/Design Artifacts/board_box_lidless.stl
8.08 x 7.50 x 3.40

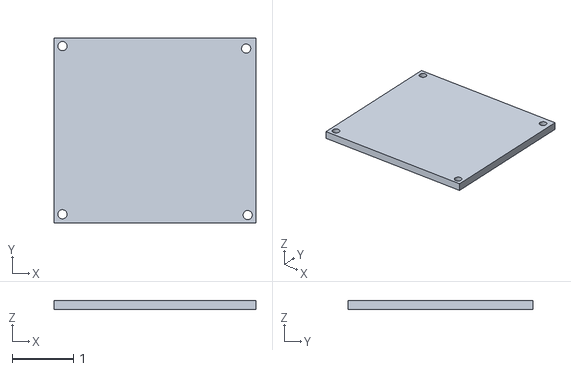
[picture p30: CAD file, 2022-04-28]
ProjectDocumentation/Design Artifacts/motor_box_lid.stl
3.30 x 3.02 x 0.15

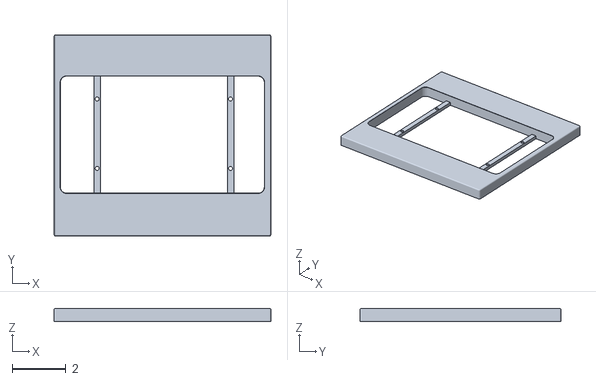
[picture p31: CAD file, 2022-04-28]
Project_Documentation/Design Artifacts/board_box_lid.stl
8.08 x 7.50 x 0.483

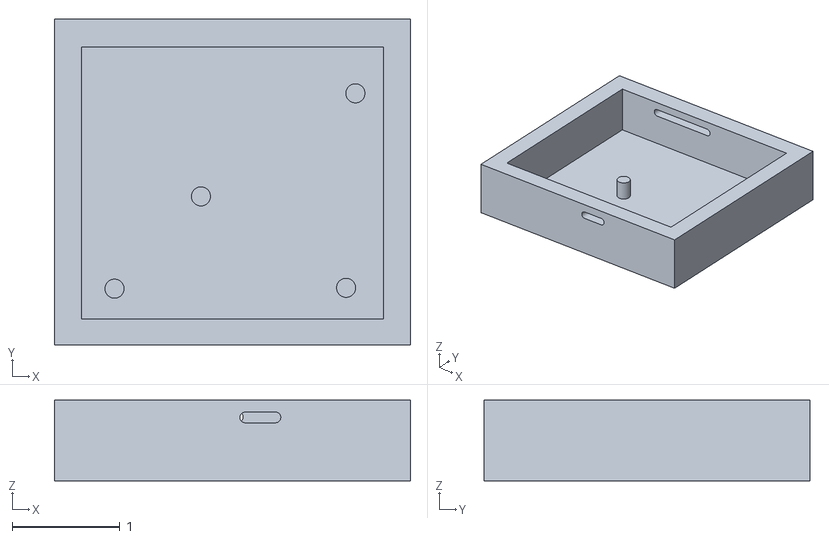
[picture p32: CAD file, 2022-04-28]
Project_Documentation/Design Artifacts/motor_box.stl
3.30 x 3.02 x 0.75

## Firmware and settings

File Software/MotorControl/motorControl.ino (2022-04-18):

int vibrationRead = 1;
int val = 0;
int val2 = 0;
int test = 0;

void setup() {
  // put your setup code here, to run once:
   TCCR2B = TCCR2B & B11111000 | B00000110; // Freq 61.04 Hz
   pinMode(6, OUTPUT); // (Use D6 for voltage output)
   pinMode(A0, INPUT); // Voltage IN
   pinMode(A1, INPUT); // Current IN


   Serial.begin(9600);
}

void loop() {
  // Old code to read in voltage and current from motor control board, not needed anymore
  /*val = analogRead(A0); //Read pin A0 voltage (Use for voltage input)
  Serial.println(val); //Check serial monitor for value and voltage
  Serial.print("Voltage: ");
  Serial.println(((float(val)*5)/1024));

  val2 = analogRead(A1); //Read pin A0 voltage (Use for voltage input)
  Serial.println(val2); //Check serial monitor for value and voltage
  Serial.print("Amps: ");
  Serial.println(((float(val)*1.75)/1024));*/
  
 while(1){
    // This code is to read in serial from RPi, not used due to explanation in readme
    /*if(Serial.available() > 0){
      String data = Serial.readStringUntil('\n');
    }*/
    if(vibrationRead == 1){
      digitalWrite(6, HIGH); //VRMS = 1.5 V
      delay(10);
      digitalWrite(6, LOW);
      delay(10);
      delay(random(10000, 45000));
    }
   }
  
  // All of these change if you change the frequency, which shouldn't help anything
  // Old code for mosfet gate control (PWM)
  
  //analogWrite(3, 123); //VRMS = 2 V

  //analogWrite(6, 75); //VRMS = 2.5 V
  
  //analogWrite(6, 104); //VRMS = 3 V

  //analogWrite(6, 138); //VRMS = 3.5 V

  //analogWrite(6, 177); //VRMS = 4 V

  //analogWrite(6, 224); //VRMS = 4.5 V

  //analogWrite(6, 254); //VRMS = 4.74 V
}

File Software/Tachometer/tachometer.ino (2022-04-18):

//Tachometer driver file
//Don't change baud rate of serial or it will break!!
//Delay for loop limit can be changed to speed up measurement timing

int limit = 500;

int delay1(){
  int i,j;
  unsigned int count=0;
  for(i=0;i<limit;i++){
    for(j=0;j<limit;j++){
      if(digitalRead(2) == LOW){
        count++;
        while(digitalRead(2) == LOW);
      }
    }
  }
  return count;
}

void setup(){
  Serial.begin(9600);
  pinMode(2, INPUT);
}

void loop(){
  unsigned int time=0,RPM=0;
  time=delay1();
  RPM=((time)*25)/20;
  
  Serial.print(RPM);

}

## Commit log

2022-04-16 Arduino files
2022-04-18 Arduino: Tachometer
2022-04-18 Schematics & Models
2022-04-18 Arduino: Motor
2022-04-28 Project Info
    [board_box_lidless (1).stl, board_box_lidless (2).stl, board_box_lidless (3).stl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]
